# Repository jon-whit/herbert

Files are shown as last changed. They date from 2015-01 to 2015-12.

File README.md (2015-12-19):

Documents
	- this folder contains our documentation including presentations and support material

Electronics
	- this folder contains the datasheets and schematics for the electronic boards we used

Firmware
	- this folder contains the fpga and firmware code

ImageProcessing
	- this folder contains the image processing code and the kcube application

Mechanical 
	- this folder contains the mechanical drawing for parts we designed and datasheets for parts we bought

TestApplication
	- this folder contains the code for our debug gui application we used for testing

Each of these folders contains it's own README explaining in more detail the contents

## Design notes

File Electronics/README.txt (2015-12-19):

This folder contains a directory for each of the electronic boards.  

The directories contain related schematics and datasheets for each part.

We did not design any of these boards.  We only repurposed i/o ports for our purposes.

These documents were used for reference only.

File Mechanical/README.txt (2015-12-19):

This folder contains mechanical drawings or datasheets for each of the mechanical parts we either designed or bought

The parts that we designed were:
	- RC-MECH-01 Socket
	- RC-MECH-02 Sensor Mount
	- RC-MECH-07 Pin
	- RC-MECH-11 Back Plate
	- RC-MECH-20 Bearing Plateform
	- RC-MECH-21 Solenoid Valve Mount

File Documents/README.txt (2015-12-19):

The "Documents" directory contains all of the documents that we created or
collected over the course of this project. This includes presentations, proposals,
and any material that we referenced for the design of our project.

--------
FPGADocs
--------
A directory containing a PDF that we used to help us program the Microblaze
processor on the FPGA.

----------
GroupNotes
----------
A directory that contains group meeting notes between January and February. We
switched over to Hansoft during the summer, and then we started emailing you with
progress updates this semester.

------
Images
------
A directory containing all of the images and models of our system that were used
in our presentations, proposal, and final report.

-------------
Presentations
-------------
Contains our initial presentation (ECE 3992) and our final presentation, along with
the supporting material for these presentations.

------
Videos
------
Contains a few videos highlighting the progress of the system over time.

--------
main.tex
--------
Our final presentation

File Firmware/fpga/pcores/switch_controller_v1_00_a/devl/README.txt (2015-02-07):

TABLE OF CONTENTS
  1) Peripheral Summary
  2) Description of Generated Files
  3) Description of Used IPIC Signals
  4) Description of Top Level Generics

================================================================================
*                             1) Peripheral Summary                            *
================================================================================
Peripheral Summary:

  XPS project / EDK repository               : C:\Git\herbert\Firmware\fpga
  logical library name                       : switch_controller_v1_00_a
  top name                                   : switch_controller
  version                                    : 1.00.a
  type                                       : PLB (v4.6) slave
  features                                   : slave attachment
                                               user s/w registers

Address Block for User Logic and IPIF Predefined Services

  user logic slave space                     : C_BASEADDR + 0x00000000
                                             : C_BASEADDR + 0x000000FF

================================================================================
*                          2) Description of Generated Files                   *
================================================================================
- HDL source file(s)

  hdl/vhdl/switch_controller.vhd

    This is the template file for your peripheral's top design entity. It
    configures and instantiates the corresponding design units in the way you
    indicated in the wizard GUI and hooks it up to the stub user logic where
    the actual functionalites should get implemented. You are not expected to
    modify this template file except certain marked places for adding user
    specific generics and ports.

  vhdl/user_logic.vhd

    This is the template file for the stub user logic design entity, either in
    VHDL or Verilog, where the actual functionalities should get implemented.
    Some sample code snippet may be provided for demonstration purpose.

- XPS interface file(s)

  data/switch_controller_v2_1_0.mpd

    This Microprocessor Peripheral Description file contains information of the
    interface of your peripheral, so that other EDK tools can recognize your
    peripheral.

  data/switch_controller_v2_1_0.pao

    This Peripheral Analysis Order file defines the analysis order of all the HDL
    source files that are used to compile your peripheral.

- ISE project file(s)

  devl/projnav/switch_controller.ise

    This is the ProjNavigator project file. It sets up the needed logical
    libraries and dependent library files for you to help you develop your
    peripheral using ProjNavigator.

  devl/projnav/switch_controller.cli

    This is the TCL command line file used to generate the .ise file.

- XST synthesis file(s)

  devl/synthesis/switch_controller_xst.scr

    This is the XST synthesis script file to compile your peripheral.
    Note: you may want to modify the device part option for your target.

  devl/synthesis/switch_controller_xst.prj

    This is the XST synthesis project file used by the above script file to
    compile your peripheral.

- Driver source file(s)

  src/switch_controller.h

    This is the software driver header template file, which contains address offset of
    software addressable registers in your peripheral, as well as some common masks and
    simple register access macros or function declaration.

  src/switch_controller.c

    This is the software driver source template file, to define all applicable driver
    functions.

  src/switch_controller_selftest.c

    This is the software driver self test example file, which contain self test example
    code to test various hardware features of your peripheral.

  src/Makefile

    This is the software driver makefile to compile drivers.

- Driver interface file(s)

  data/switch_controller_v2_1_0.mdd

    This is the Microprocessor Driver Definition file.

  data/switch_controller_v2_1_0.tcl

    This is the Microprocessor Driver Command file.

- Other misc file(s)

  devl/ipwiz.opt

    This is the option setting file for the wizard batch mode, which should
    generate the same result as the wizard GUI mode.

  devl/README.txt

    This README file for your peripheral.

  devl/ipwiz.log

    This is the log file by operating on this wizard.

================================================================================
*                         3) Description of Used IPIC Signals                  *
================================================================================
For more information (usage, timing diagrams, etc.) regarding the IPIC signals
used in the templates, please refer to the following specifications (under
%XILINX_EDK%\doc for windows or $XILINX_EDK/doc for solaris and linux):
proc_ip_ref_guide.pdf - Processor IP Reference Guide (chapter 4 IPIF)
user_core_templates_ref_guide.pdf - User Core Templates Reference Guide

Bus2IP_Clk
    Synchronization clock provided to the user logic. All IPIC signals are 
    synchronous to this clock. It is identical to the input <bus>_Clk signal of 
    the peripheral. No additional buffering is provided on the clock; it is 
    passed through as is. 

Bus2IP_Reset
    Active high reset for used by the user logic; it is asserted whenever the 
    <bus>_Rst signal asserts or whenever there is a software-programmed reset 
    (if the soft reset block is included). 

Bus2IP_Data
    Write data bus to the user logic. Write data is accepted by the user logic 
    during a write operation by assertion of the write acknowledgement signal 
    and the rising edge of the Bus2IP_Clk. 

Bus2IP_BE
    Byte Enable qualifiers for the requested read or write operation to the user 
    logic. A bit in the Bus2IP_BE set to '1' indicates that the associated byte 
    lane contains valid data. For example, if Bus2IP_BE = 0011, this indicates 
    that byte lanes 2 and 3 contains valid data. 

Bus2IP_RdCE
    Active high chip enable bus to the user logic. These chip enables are 
    asserted only during active read transaction requests with the target 
    address space and in conjunction with the corresponding sub-address within 
    the space. Typically used for user logic readable registers selection. 

Bus2IP_WrCE
    Active high chip enable bus to the user logic. These chip enables are 
    asserted only during active write transaction requests with the target 
    address space and in conjunction with the corresponding sub-address within 
    the space. Typically used for user logic writable registers selection. 

IP2Bus_Data
    Output read data bus from the user logic; data is qualified with the 
    assertion of IP2Bus_RdAck signal and the rising edge of the Bus2IP_Clk. 

IP2Bus_RdAck
    Active high read data qualifier providing the read acknowledgement from the 
    user logic. Read data on the IP2Bus_Data bus is deemed valid at the rising 
    edge of the Bus2IP_Clk and IP2Bus_RdAck asserted high by the user logic. For 
    immediate acknowledgement (such as for a register read), this signal can be 
    tied to '1'. Wait states can be inserted in the transaction by delaying the 
    assertion of the acknowledgement. 

IP2Bus_WrAck
    Active high write data qualifier providing the write acknowledgement from 
    the user logic. Write data on the Bus2IP_Data bus is deemed accepted by the 
    user logic at the rising edge of the Bus2IP_Clk and IP2Bus_WrAck asserted 
    high by the user logic. For immediate acknowledgement (such as for a 
    register write), this signal can be tied to '1'. Wait states can be inserted 
    in the transaction by delaying the assertion of the acknowledgement. 

IP2Bus_Error
    Active high signal indicating the user logic has encountered an error with 
    the requested operation. It is asserted in conjunction with the read/write 
    acknowledgement signal(s). 

================================================================================
*                     4) Description of Top Level Generics                     *
================================================================================
C_BASEADDR/C_HIGHADDR
    These two generics are used to define the memory mapped address space for
    the peripheral registers, including Soft Reset register, Interrupt Source
    Controller registers, Read/Write FIFO control/data registers, user logic
    software accessible registers and etc., but excluding those user logic
    memory spaces if ever existed. When instantiation, the address space
    size determined by these two generics must be a power of 2 (e.g. 2^k =
    C_HIGHADDR - C_BASEADDR + 1), a factor of C_BASEADDR and larger than the
    minimum size as indicated in the template.

C_SPLB_AWIDTH
    This is the slave interface address bus width for Processor Local Bus
    version 4.6 (PLBv46). Value can be assigned automatically by EDK
    tooling during system creation.

C_SPLB_DWIDTH
    This is the slave interface data bus width for Processor Local Bus
    version 4.6 (PLBv46). Value can be assigned automatically by EDK
    tooling during system creation.

C_SPLB_NUM_MASTERS
    This indicates to the slave interface the number of PLBv46 masters
    present. Value can be assigned automatically by EDK tooling during
    system creation.

C_SPLB_MID_WIDTH
    This indicates to the slave interface the number of bits required
    for the PLB_masterID input bus. It is an integer value equal to
    log2(C_SPLB_NUM_MASTERS). Value will be assigned automatically by
    EDK tooling during system creation.

C_SPLB_NATIVE_DWIDTH
    This indicates to the slave interface the native bit width of the
    internal data bus of the peripheral. Some peripheral will require
    the value of this parameter to be fixed, while others might have
    selectable native data widths.

C_SPLB_P2P
    This indicates to the slave interface when it is exclusively attached
    to a PLBv46 bus via a Point to Point interconnect scheme. In this
    scenario, the slave interface may be able to reduce resource utilization
    by eliminating address decode function and modifying interface behavior
    to allow for a reduction in latency.

C_SPLB_SUPPORT_BURSTS
    This indicates to the associated PLBv46 bus that this slave interface
    support burst transfers to improve performance.

C_SPLB_SMALLEST_MASTER
    This indicates the smallest native data width of any master on the
    corresponding PLBv46 bus that may access the slave interface. It allows
    optimizations within the slave interface logic if narrower masters don't
    have to be supported for that application.

C_SPLB_CLK_PERIOD_PS
    This is the period of the PLBv46 bus clock (in picoseconds) for the
    corresponding PLBv46 slave interface attachment. It has been defined
    for use by peripheral that needs to know the bus clock rate to improve
    certain functions such as internal timers.

C_INCLUDE_DPHASE_TIMER
    This indicates if the data phase timer is used or not. The value of
    0 will exclude the timer.  The value of 1 includes the timer.
    If C_INCLUDE_DPHASE_TIMER = 1 and after 128 SPLB_Clk cycles, as
    measured from the assertion of Sl_AddrAck, the User IP does not
    respond with either an IP2Bus_RdAck or IP2Bus_WrAck the 
    plbv46_slave_single will de-assert the User IP cycle request
    signals, Bus2IP_CS and Bus2IP_RdCE or Bus2IP_WrCE, and will assert
    Sl_rdDAck with Sl_rdDBus=zero for a read cycle or Sl_wrDAck for
    a write cycle. This will gracefully terminate the cycle. Note 
    that the requesting master will have no knowledge that the data
    phase of the PLB request was terminated in this manner.

C_FAMILY
    This is to set the target FPGA architecture, s.t. virtex5, etc.

================================================================================
*          5) Location to documentation of dependent libraries                 *
*                                                                              *
*   In general, the documentation is located under:                            *
*   $XILINX_EDK/hw/XilinxProcessorIPLib/pcores/$libName/doc                    *
*                                                                              *
================================================================================
proc_common_v2_00_a
	No documentation for this library

plbv46_slave_single_v1_00_a
	C:\Git\herbert\Firmware\fpga\C:\Xilinx\10.1\EDK\hw\XilinxProcessorIPLib\pcores\plbv46_slave_single_v1_00_a\doc\plbv46_slave_single.pdf

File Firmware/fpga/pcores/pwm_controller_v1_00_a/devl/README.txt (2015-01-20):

TABLE OF CONTENTS
  1) Peripheral Summary
  2) Description of Generated Files
  3) Description of Used IPIC Signals
  4) Description of Top Level Generics

================================================================================
*                             1) Peripheral Summary                            *
================================================================================
Peripheral Summary:

  XPS project / EDK repository               : C:\Development\Sandbox\Projects\PlateCycler\Alpha\Firmware\S3DevBoard
  logical library name                       : pwm_controller_v1_00_a
  top name                                   : pwm_controller
  version                                    : 1.00.a
  type                                       : PLB (v4.6) slave
  features                                   : slave attachment
                                               interrupt control
                                               user s/w registers

Address Block for User Logic and IPIF Predefined Services

  user logic slave space                     : C_BASEADDR + 0x00000000
                                             : C_BASEADDR + 0x000000FF
  interrupt control space                    : C_BASEADDR + 0x00000100
                                             : C_BASEADDR + 0x000001FF

================================================================================
*                          2) Description of Generated Files                   *
================================================================================
- HDL source file(s)

  hdl/vhdl/pwm_controller.vhd

    This is the template file for your peripheral's top design entity. It
    configures and instantiates the corresponding design units in the way you
    indicated in the wizard GUI and hooks it up to the stub user logic where
    the actual functionalites should get implemented. You are not expected to
    modify this template file except certain marked places for adding user
    specific generics and ports.

  vhdl/user_logic.vhd

    This is the template file for the stub user logic design entity, either in
    VHDL or Verilog, where the actual functionalities should get implemented.
    Some sample code snippet may be provided for demonstration purpose.

- XPS interface file(s)

  data/pwm_controller_v2_1_0.mpd

    This Microprocessor Peripheral Description file contains information of the
    interface of your peripheral, so that other EDK tools can recognize your
    peripheral.

  data/pwm_controller_v2_1_0.pao

    This Peripheral Analysis Order file defines the analysis order of all the HDL
    source files that are used to compile your peripheral.

- ISE project file(s)

  devl/projnav/pwm_controller.ise

    This is the ProjNavigator project file. It sets up the needed logical
    libraries and dependent library files for you to help you develop your
    peripheral using ProjNavigator.

  devl/projnav/pwm_controller.cli

    This is the TCL command line file used to generate the .ise file.

- XST synthesis file(s)

  devl/synthesis/pwm_controller_xst.scr

    This is the XST synthesis script file to compile your peripheral.
    Note: you may want to modify the device part option for your target.

  devl/synthesis/pwm_controller_xst.prj

    This is the XST synthesis project file used by the above script file to
    compile your peripheral.

- Driver source file(s)

  src/pwm_controller.h

    This is the software driver header template file, which contains address offset of
    software addressable registers in your peripheral, as well as some common masks and
    simple register access macros or function declaration.

  src/pwm_controller.c

    This is the software driver source template file, to define all applicable driver
    functions.

  src/pwm_controller_selftest.c

    This is the software driver self test example file, which contain self test example
    code to test various hardware features of your peripheral.

  src/Makefile

    This is the software driver makefile to compile drivers.

- Driver interface file(s)

  data/pwm_controller_v2_1_0.mdd

    This is the Microprocessor Driver Definition file.

  data/pwm_controller_v2_1_0.tcl

    This is the Microprocessor Driver Command file.

- Other misc file(s)

  devl/ipwiz.opt

    This is the option setting file for the wizard batch mode, which should
    generate the same result as the wizard GUI mode.

  devl/README.txt

    This README file for your peripheral.

  devl/ipwiz.log

    This is the log file by operating on this wizard.

================================================================================
*                         3) Description of Used IPIC Signals                  *
================================================================================
For more information (usage, timing diagrams, etc.) regarding the IPIC signals
used in the templates, please refer to the following specifications (under
%XILINX_EDK%\doc for windows or $XILINX_EDK/doc for solaris and linux):
proc_ip_ref_guide.pdf - Processor IP Reference Guide (chapter 4 IPIF)
user_core_templates_ref_guide.pdf - User Core Templates Reference Guide

Bus2IP_Clk
    Synchronization clock provided to the user logic. All IPIC signals are 
    synchronous to this clock. It is identical to the input <bus>_Clk signal of 
    the peripheral. No additional buffering is provided on the clock; it is 
    passed through as is. 

Bus2IP_Reset
    Active high reset for used by the user logic; it is asserted whenever the 
    <bus>_Rst signal asserts or whenever there is a software-programmed reset 
    (if the soft reset block is included). 

Bus2IP_Data
    Write data bus to the user logic. Write data is accepted by the user logic 
    during a write operation by assertion of the write acknowledgement signal 
    and the rising edge of the Bus2IP_Clk. 

Bus2IP_BE
    Byte Enable qualifiers for the requested read or write operation to the user 
    logic. A bit in the Bus2IP_BE set to '1' indicates that the associated byte 
    lane contains valid data. For example, if Bus2IP_BE = 0011, this indicates 
    that byte lanes 2 and 3 contains valid data. 

Bus2IP_RdCE
    Active high chip enable bus to the user logic. These chip enables are 
    asserted only during active read transaction requests with the target 
    address space and in conjunction with the corresponding sub-address within 
    the space. Typically used for user logic readable registers selection. 

Bus2IP_WrCE
    Active high chip enable bus to the user logic. These chip enables are 
    asserted only during active write transaction requests with the target 
    address space and in conjunction with the corresponding sub-address within 
    the space. Typically used for user logic writable registers selection. 

IP2Bus_Data
    Output read data bus from the user logic; data is qualified with the 
    assertion of IP2Bus_RdAck signal and the rising edge of the Bus2IP_Clk. 

IP2Bus_RdAck
    Active high read data qualifier providing the read acknowledgement from the 
    user logic. Read data on the IP2Bus_Data bus is deemed valid at the rising 
    edge of the Bus2IP_Clk and IP2Bus_RdAck asserted high by the user logic. For 
    immediate acknowledgement (such as for a register read), this signal can be 
    tied to '1'. Wait states can be inserted in the transaction by delaying the 
    assertion of the acknowledgement. 

IP2Bus_WrAck
    Active high write data qualifier providing the write acknowledgement from 
    the user logic. Write data on the Bus2IP_Data bus is deemed accepted by the 
    user logic at the rising edge of the Bus2IP_Clk and IP2Bus_WrAck asserted 
    high by the user logic. For immediate acknowledgement (such as for a 
    register write), this signal can be tied to '1'. Wait states can be inserted 
    in the transaction by delaying the assertion of the acknowledgement. 

IP2Bus_Error
    Active high signal indicating the user logic has encountered an error with 
    the requested operation. It is asserted in conjunction with the read/write 
    acknowledgement signal(s). 

IP2Bus_IntrEvent
    The IP2Bus_IntrEvent bus is an output from the user logic to the IPIF that 
    consists of interrupt event signals to be detected and latched inside the 
    IPIF. 

================================================================================
*                     4) Description of Top Level Generics                     *
================================================================================
C_BASEADDR/C_HIGHADDR
    These two generics are used to define the memory mapped address space for
    the peripheral registers, including Soft Reset register, Interrupt Source
    Controller registers, Read/Write FIFO control/data registers, user logic
    software accessible registers and etc., but excluding those user logic
    memory spaces if ever existed. When instantiation, the address space
    size determined by these two generics must be a power of 2 (e.g. 2^k =
    C_HIGHADDR - C_BASEADDR + 1), a factor of C_BASEADDR and larger than the
    minimum size as indicated in the template.

C_SPLB_AWIDTH
    This is the slave interface address bus width for Processor Local Bus
    version 4.6 (PLBv46). Value can be assigned automatically by EDK
    tooling during system creation.

C_SPLB_DWIDTH
    This is the slave interface data bus width for Processor Local Bus
    version 4.6 (PLBv46). Value can be assigned automatically by EDK
    tooling during system creation.

C_SPLB_NUM_MASTERS
    This indicates to the slave interface the number of PLBv46 masters
    present. Value can be assigned automatically by EDK tooling during
    system creation.

C_SPLB_MID_WIDTH
    This indicates to the slave interface the number of bits required
    for the PLB_masterID input bus. It is an integer value equal to
    log2(C_SPLB_NUM_MASTERS). Value will be assigned automatically by
    EDK tooling during system creation.

C_SPLB_NATIVE_DWIDTH
    This indicates to the slave interface the native bit width of the
    internal data bus of the peripheral. Some peripheral will require
    the value of this parameter to be fixed, while others might have
    selectable native data widths.

C_SPLB_P2P
    This indicates to the slave interface when it is exclusively attached
    to a PLBv46 bus via a Point to Point interconnect scheme. In this
    scenario, the slave interface may be able to reduce resource utilization
    by eliminating address decode function and modifying interface behavior
    to allow for a reduction in latency.

C_SPLB_SUPPORT_BURSTS
    This indicates to the associated PLBv46 bus that this slave interface
    support burst transfers to improve performance.

C_SPLB_SMALLEST_MASTER
    This indicates the smallest native data width of any master on the
    corresponding PLBv46 bus that may access the slave interface. It allows
    optimizations within the slave interface logic if narrower masters don't
    have to be supported for that application.

C_SPLB_CLK_PERIOD_PS
    This is the period of the PLBv46 bus clock (in picoseconds) for the
    corresponding PLBv46 slave interface attachment. It has been defined
    for use by peripheral that needs to know the bus clock rate to improve
    certain functions such as internal timers.

C_FAMILY
    This is to set the target FPGA architecture, s.t. virtex5, etc.

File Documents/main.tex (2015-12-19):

% pre-amble section
\documentclass[final, letterpaper, 10 pt, conference, twocolumn]{IEEEtran}

\usepackage[utf8]{inputenc}
\usepackage{geometry}
\usepackage{hyperref}
\usepackage{graphicx}
\graphicspath{ {Images/} }
\usepackage{listings}
\usepackage{xcolor}
\usepackage{fancyvrb}
\usepackage[backend=bibtex]{biblatex}

\bibliography{references.bib}

\lstdefinestyle{DOS}
{
    backgroundcolor=\color{black},
    basicstyle=\scriptsize\color{white}\ttfamily
}

\title{Herbert\\Autonomous Robotic Rubik's Cube Solver}
\author{
    Jonathan Whitaker, Dylan Lytle, Matt Frandsen, Li Lao\\
    \textit{Dept. of Electrical and Computer Engineering, University of Utah}\\
}

\date{December 2015}
% end of pre-amble

% document content
\begin{document}

\maketitle

\begin{abstract}
Project Herbert is an autonomous robotic Rubik's Cube solver that is composed of a complex network of mechanical and electrical devices. In this project our team interfaced with these complex mechanical and electrical devices so as to design and create an autonomous robot that is capable of solving a Rubik's cube within two minutes of time.  This project is an integration of various technologies including: mechanical actuators, electrical stepper motors, single-board computers, field-programmable gate arrays, and video cameras.
\end{abstract}

\section{Introduction}
\label{sec:intro}
The goal of this project was to create an autonomous robotic Rubik's Cube solver through the integration of several components. The main components integrated into our project include video cameras, electrical stepper motors, mechanical actuators, a single-board computer (SBC), and field-programmable gate arrays (FPGAs). A video camera connects to the computer through standard universal serial bus (USB) 2.0 protocol \cite{USB2.0}. The video camera is responsible for capturing the initial configuration of the Rubik's Cube, and the single board computer is responsible for processing the video frame information and generating a matrix model for the initial state of the cube. After generating a matrix model for the initial cube, the computer applies Kociemba's algorithm \cite{Kociemba} (an optimal algorithm used to solve a Rubik's Cube) to generate a solution sequence that can be processed sequentially. The solution sequence that Kociemba's algorithm returns is in the standard notation used in Rubik's Cube discussion and theory (see Appendix \ref{sec:Appendix A}). As each solution sequence is processed, the computer communicates through an RS232 serial connection to an FPGA control board which drives the mechanical actuations and stepper motor rotations needed to physically manipulate the cube. The FPGA acts as a system control board and is responsible for controlling the actions of two motor control boards and a relay board used to trigger the mechanical actuators. An overview of this process can be found below in Fig. \ref{fig:System Block Diagram}.

\begin{figure*}[!ht]
\centering

\caption{Herbert Block Diagram}
\label{fig:System Block Diagram}
\end{figure*}

\begin{figure}[!ht]
\centering

\caption{Initial ideal cube image capture}
\label{fig:Camera Positioning}
\end{figure}

\section{Software Implementation}
\label{sec:Software Implementation}
The single board computer in our system operates a software stack composed of Python, Cython, and OpenCV. We utilized a 3rd party Python library called \textit{pyflycapture2} \cite{pyflycapture2} to capture images from the camera that was provided to us by Point Grey Research. Once the images of the cube are captured, we apply color recognition and categorization using OpenCV-Python \cite{OpenCVPython}. The characterization phase in OpenCV generates a matrix model of the Rubik's cube. We pass this matrix model on to an application called Kcube to generate a solution sequence needed to solve the cube permutation. We go into each these components in more detail in the next few sections.

\subsection{Image Processing}
The image processing aims to capture the initial state of the cube using a camera. The criteria for evaluating the success of the image processing implementation is robustness and speed of the algorithm.

\begin{figure}[!hb]
\centering
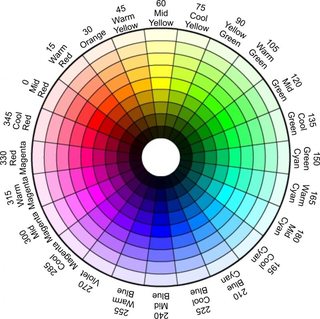
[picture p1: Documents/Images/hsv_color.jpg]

\caption{HSV color wheel}
\label{fig:HSV}
\end{figure}

\subsubsection{Point Grey Camera and FlyCapture Software Development Kit}
We interfaced with the cameras using Point Grey's API, which was provided to us through the FlyCapture software development kit (SDK) \cite{FlyCapture}. The FlyCapture SDK was implemented in C. Since we chose to use Python as our base language, we had to use Cython, an optimized static compiler for C extensions in Python. We use Cython to bind the C functions within the FlyCapture API to Python functions.  The FlyCapture SDK  provided us with a large amount of configurability, and it gave us a flexible interface for which the cameras settings could be adjusted to enhance capturing mode and synchronizing image buffer retrieval.

We initially had planned to use two cameras, each connected to the SBC through a standard USB 2.0 connection. Each one of these cameras was going to be responsible for capturing exactly three of the six faces of the cube with a view like that shown in Fig. \ref{fig:Camera Positioning}. However, as construction of the main frame of our project came to a close, we soon realized that various parts of the mechanical system obscured the view of a large majority of the facelets on the three faces. On top of this, we also experienced challenges dealing with color recognition in ambient lighting. Because of these challenges we decided that our original camera configuration was not ideal.

We decided to compromise and use a single camera configuration. A single camera is used to capture the entire state of a Rubik's Cube. The single camera was best positioned like that shown in Fig. \ref{fig:Obscured Cube}. A static mechanical rotation sequence is used to capture the cube in various configurations until all of the facelets on the cube are captured. The cube is then returned to its original state, and the collection of images are saved off for facelet characterization.

\subsubsection{Cube Orientation} 
The pixel region of each of the facelets  must be identified for color recognition. We initially planned on using a combination of grayscale conversion and contour filtering to dynamically detect a bounding contour around each of the facelets. However, the dynamic approach to identifying a facelet pixel region proved to be difficult due to the lack of vision of the cube. The arm assemblies were too obtrusive to capture a clean image (see Fig. \ref{fig:Obscured Cube}).

Because the camera and the Rubik's Cube remains fixed inside the mechanical frame, we decided to implement a static solution. Through a GUI interface, a static polygon for each of the facelets was defined. Each of the static polygons creates a bounding rectangle around a facelet pixel region. The static solution that we adopted proved to be consistent, but it necessitated high maintenance. Each of the static polygons must be redefined each time the camera position changes or if a mechanical change affects the orientation of the cube. If we were to continue on with this project, this is one aspect that we could improve. It would be nice to implement a robust dynamic approach.

\begin{figure}[!h]
\centering
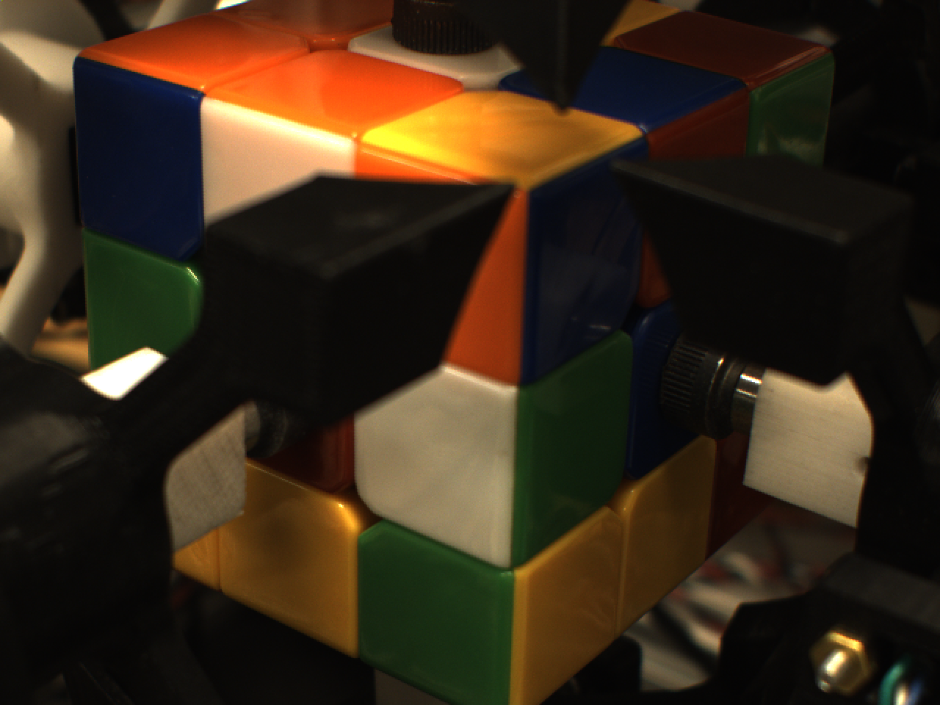
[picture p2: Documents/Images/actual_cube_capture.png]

\caption{Obscured cube image capture}
\label{fig:Obscured Cube}
\end{figure}

\subsubsection{Color Space}
Lighting condition severally affects the robustness of the color recognition algorithm. Color values on a Rubik's Cube facelet drastically change if the facelet is reflective or if a shadow is cast upon it. This proved to be challenging for us. However, we were able to maintain a consistent lighting around the mechnical frame to mitigate a majority of these problems. We were very confident in the color recognition algorithm under normal lighting conditions. During demo day, we solved over 24 Rubik's Cubes without failure.

Choosing a color space that was robust to lighting conditions was critical to enabling a robust color recognition algorithm. Several color spaces such as RGB, CMYK, and HSV were examined. The HSV color space provided the best consistency under various lighting conditions. The three components of the HSV color space are hue, saturation, and value. The hue component describes the similarity of the color to an unique hue: red, green, blue, and yellow as shown in Fig. \ref{fig:HSV}. The saturation component measures the intensity or ``colorfulness" of the specific hue. Finally, the value measures the brightness of the color value. HSV is ideal for developing a robust color recognition because shadows and high gloss merely change the value component of the color without affecting the hue and saturation component of the color. Additionally, the hue component can be used to distinctly distinguish each of the primary colors such as red, green, and blue that are found on a Rubik's Cube facelet.

\begin{figure}[!ht]
\centering
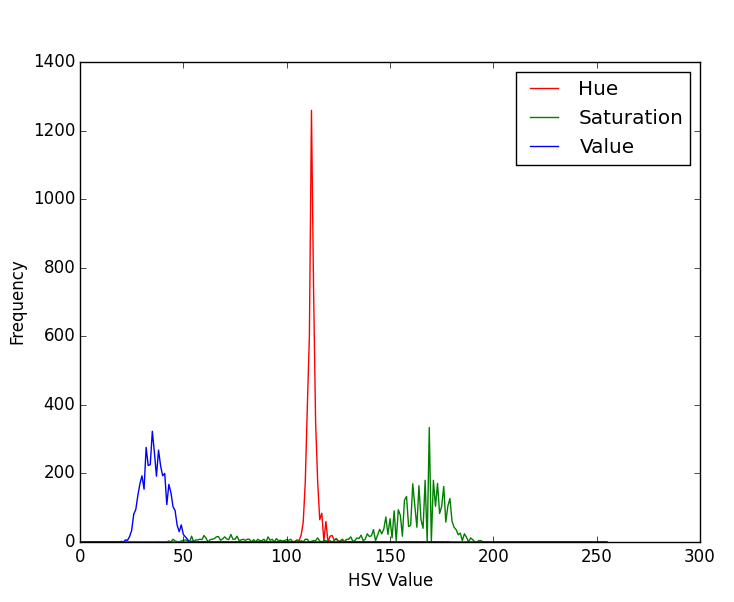
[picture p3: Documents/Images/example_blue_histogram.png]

\caption{Example HSV color histogram for blue}
\label{fig:Example Histogram}
\end{figure}

\begin{table}[!ht]
\caption{HSV color ranges}
\label{table:color ranges}
\centering
\begin{tabular}{|c|c|c|}
\hline
\textbf{COLOR} & \textbf{HUE} & \textbf{SATURATION} \\ \hline
WHITE          & 25 - 58  & 0 - 139               \\ \hline
RED            & 1  - 12     & 0 - 255            \\ \hline
BLUE           & 200 - 280   & 0 - 255              \\ \hline
GREEN          & 80 - 120   & 0 - 255            \\ \hline
ORANGE         & 15 - 20     & 0 - 255         \\ \hline
YELLOW         & 25 - 58   & 140 - 255            \\ \hline
\end{tabular}
\end{table}

\subsubsection{Categorization Algorithm}
After identifying a bounding contour around each of the facelets, a categorization algorithm was used to determine the color contained within the bounding rectangle. Each image was first converted to the HSV color space. The hue and saturation components of each pixel value is then used to categorize the color. Several color histograms such as the one shown in Fig. \ref{fig:Example Histogram} were constructed for each facelet and were used to determine the ranges of each HSV component in order to categorize a single facelet color. For example, the histogram shown in Fig. \ref{fig:Example Histogram} was constructed for a blue facelet. The hue values range between 100 to 130 and the saturation values ranges from 150 to 180. Our analysis led to the resulting HSV ranges shown in Table. \ref{table:color ranges}.

Based on these color ranges, the categorization algorithm can be implemented based on the average of all the pixel values in the facelet region or the frequency of each pixel value. A categorization algorithm based on the average of HSV values proved to be quick, but it was also error-prone due to outliers. A categorization algorithm based on frequency of each HSV component proved to be more robust, but less optimized. Our final implementation computes a histogram of the facelet pixel region using OpenCV. Based on the histogram, the frequency of each of the facelet colors is determined. The highest frequency of a facelet color determines the color that facelet is binned into.

Our initial trivial algorithm that we implemented took approximately a minute to categorize each facelet, because of the unoptimized looping in Python and hardware limitations. After several iterative optimizations using the OpenCV library, the overall color categorization time was reduced to approximately three seconds.  In the future, the categorization can still be optimized for both robustness and speed. For example, the image resolution or the overall pixel region can be reduced to improve performance. Additionally, a filtering algorithm can be used to reduce the effects on abnormal lighting. 

\subsection{Kcube and the Solution Sequence}
\begin{figure*}[!ht]
\begin{center}
\begin{BVerbatim}
             |************|
             |*U1**U2**U3*|
             |************|
             |*U4**U5**U6*|
             |************|
             |*U7**U8**U9*|
             |************|
|************|************|************|************|
|*L1**L2**L3*|*F1**F2**F3*|*R1**R2**F3*|*B1**B2**B3*|
|************|************|************|************|
|*L4**L5**L6*|*F4**F5**F6*|*R4**R5**R6*|*B4**B5**B6*|
|************|************|************|************|
|*L7**L8**L9*|*F7**F8**F9*|*R7**R8**R9*|*B7**B8**B9*|
|************|************|************|************|
             |************|
             |*D1**D2**D3*|
             |************|
             |*D4**D5**D6*|
             |************|
             |*D7**D8**D9*|
             |************|
\end{BVerbatim}
\end{center}
\caption{Rubik's Cube matrix representation}
\label{fig:matrix layout}
\end{figure*}

\begin{table}[!ht]
\caption{Cubelet color to ASCII character mapping}
\label{table:cubelet representation}
\centering
\begin{tabular}{|c|c|}
\hline
\textbf{COLOR} & \textbf{CHARACTER} \\ \hline
WHITE          & `W'              \\ \hline
RED            & `R'              \\ \hline
BLUE           & `B'              \\ \hline
GREEN          & `G'              \\ \hline
ORANGE         & `O'              \\ \hline
YELLOW         & `Y'              \\ \hline
\end{tabular}
\end{table}

\label{sec:Kcube}
Kcube is a C++ application developed by Greg Schmidt that utilizes Kociemba's two-phase algorithm which uses two stages of an iterative depth first search algorithm \cite{TheTwo-PhaseAlgorithm}. We utilized the Kcube application to generate the solution sequence needed to solve the Rubik's Cube that was captured during the image processing phase. The matrix model generated from the image processing phase allows us to provide Kcube's command-line interface with the cube representation needed to generate a solution sequence. Kcube's command-line interface takes six parameters, one for each face of the cube. The values for these parameters are the color characters at each of the cubelet locations for that face (as seen in Fig. \ref{fig:matrix layout}). For example, to solve the scrambled cube shown in Fig. \ref{fig:scrambled cube} you invoke Kcube with the following command:

\begin{lstlisting}[style=DOS]
c:>kcube L:GGWWOWBRB
         F:GWGBGYWBO
         U:YOOOWYROY
         D:ORGWYYYRB
         R:OGBBRYWRR
         B:YBROBGWGR
\end{lstlisting}

Kcube processes the input parameters and generates a sequence of twenty-three or less moves (see Appendix \ref{sec:fundamental moves}) that, when applied to the cube, will solve the cube. Each move is mapped to a unique character or set of characters (see Table \ref{table:moves table}), and these characters are transmitted over an RS232 serial connection to the FPGA control board, at which point the control board takes responsibility for controlling the electro-mechanical stepper motors and mechanical actuators needed to physically manipulate the cube.

\begin{figure}[!hb]
\centering

\caption{A scrambled cube}
\label{fig:scrambled cube}
\end{figure}

\begin{table}[!ht]
\caption{Cube moves to character set mapping}
\label{table:moves table}
\centering
\begin{tabular}{|c|c|c|c|c|c|}
\hline
\textbf{MOVE} & \textbf{CHAR} & \textbf{MOVE} & \textbf{CHAR} & \textbf{MOVE} & \textbf{CHAR} \\ \hline
F             & F              & R             & R              & D             & D             \\ \hline
F'            & Fb              & R'            & Rb              & D'            & Db            \\ \hline
F2            & F2              & R2            & R2              & D2            & D2             \\ \hline
L             & L              & U             & U             & B             & B             \\ \hline
L'            & Lb              & U'            & Ub             & B'            & Bb             \\ \hline
L2            & L2              & U2            & U2             & B2            & B2             \\ \hline
\end{tabular}
\end{table}

\section{Hardware Implementation}
\subsection{Mechanical Actuators}
\label{sec:Mechanical Actuators}
Herbert employs a six arm design to physically manipulate the cube. One arm for each face of the cube. In order to achieve a six arm design, each arm actuates in and out so as to avoid conflict
with the other arms. This actuation process is a time critical component of
the design.  We initially planned on implementing the
arm actuation with motors.  However, preliminary testing showed that using
motors to convert rotary motion into linear motion is too slow, and using a linear motor
actuator is too costly. We decided that pneumatic actuation is the solution to this problem.  Each of the arms is attached to a double action pneumatic air cylinder as show in Fig. \ref{fig:Pneumatic Air Cylinder}.

The FPGA control board is responsible for controlling a relay control board (see Fig. \ref{fig:System Block Diagram}) which controls coaxial pairs of air cylinders. The actuation distance for each control arm is fixed. The coaxial pairs of arms are kept in an extended or retracted position, depending on the current move being executed. Potential optimizations and more stable cube manipulations  are obtained by simultaneously extending and retracting coaxial pairs of arms. The linear actuation motion allows a coaxial pair of
arms to extend, thus encasing two sides of the cube in the sockets of the arms. After a pair of arms extend,
a stepper motor spins the arm corresponding to the appropriate move from the solution sequence (see section \ref{sec:Stepper Motors}). Each air cylinder is provided approximately 40-60 psi supplied from an air compressor. To protect against any arm collisions, only one pair of arms is in the extended position at any given time.

Initially our design incorporated mechanical switches that would be triggered by physical contact of the arm assembly.  These switches were mounted on the assembly in such a way that contact would occur in either the extended or retracted arm positions.  The goal of the switch based design was to remove an element of manual timing approximation.  By using the switches we would know the position of each arm at all times.  Taking advantage of this, there would be a much smaller hard coded delay, or potentially no delay.  However, due to time constraints as well as accuracy issues because of inconsistent and difficult mounting, we chose not to implement the switches in the final design.   
 
If we were to continue the project there are many improvements and optimizations that could be made. The first optimization would be to implement the switch design we initially planned on.  Improving the robustness of the switches would help reduce the time the mechanical motion takes. This would reduce the overall time to completion, because the mechanical motion is the most time intensive component of the solution. 
Another mechanical optimization that would help reduce the time to completion is to modify the arm.  The image processing was a very difficult component of this project, because the arm assembly was obtrusive to the view of the cube for the cameras.  Our thought is to remove two of the four prongs of each arm.  This modification would give the cameras a more clear view of the cube, as well as potentially giving us the ability to actuate in and out more quickly, because potential arm collisions would be reduced.

\begin{figure}[!ht]
\centering
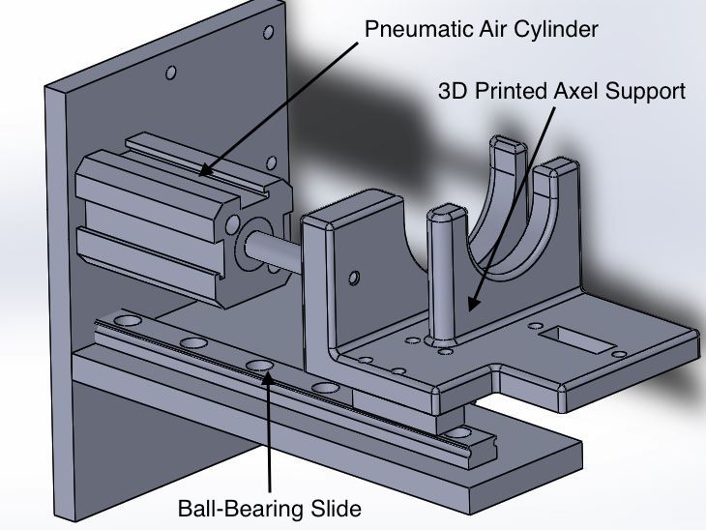
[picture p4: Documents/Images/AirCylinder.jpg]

\caption{Pneumatic Air Cylinder and 3D Printed Axel Support}
\label{fig:Pneumatic Air Cylinder}
\end{figure}

\subsection{Electro-mechanical Stepper Motors}
\label{sec:Stepper Motors}
Each actuating arm has a stepper motor which is responsible for rotating a single face. A stepper motor rotates a face either 90 degrees or 180 degrees clockwise or counter-clockwise based on the solution move that is being processed (as specified in Appendix \ref{sec:Appendix A}). A 3D printed axle (as seen Fig. \ref{fig:Stepper Motor Arm}) is fastened to the stepper motors. This axle twists a 3D printed arm piece in order to spin a face of the Rubik's Cube.

\begin{figure}[!ht]
\centering
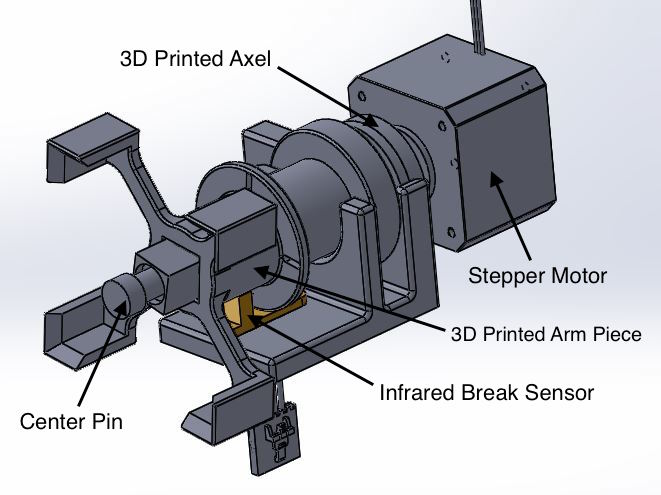
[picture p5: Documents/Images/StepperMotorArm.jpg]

\caption{Stepper Motor Arm Assembly}
\label{fig:Stepper Motor Arm}
\end{figure}

Each stepper motor is driven by a motor control board which is controlled by the FPGA control board (see Fig. \ref{fig:System Block Diagram}). The motor control boards contain a motor driver chip for each stepper motor. The FPGA control board is responsible for controlling the angular and temporal timing of each stepper motor rotation.

\subsection{Infrared Break Sensors}
\label{sec:Infrared Break Sensors}
Rotations must end at a 90 degree angle so as to not interrupt the rotation of another arm.  These exact angles are hard to accomplish by counting steps, because it is difficult to detect whether steps are skipped.  To compensate for this we used infrared break sensors like that shown in Fig. \ref{fig:Infrared Break Sensor}. Each arm assembly has an infrared sensor (see Fig. \ref{fig:Stepper Motor Arm}). The infrared sensor is broken at all angles that are not a multiple of 90 degrees. These break sensors are monitored and controlled through the motor control boards.

\begin{figure}[!ht]
\centering
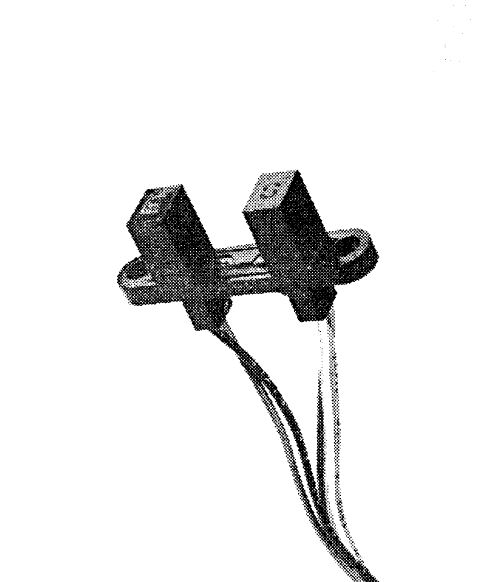
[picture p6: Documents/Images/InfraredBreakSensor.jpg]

\caption{Infrared Break Sensor}
\label{fig:Infrared Break Sensor}
\end{figure}

\subsection{Arm Progression}
\label{sec:Arm Progression}
The 3D printed arm piece at the end of each arm assembly (see Fig. \ref{fig:Stepper Motor Arm}) underwent a great progression. Fig. \ref{fig:Arm Progression} highlights the progression of the arm pieces from left to right. The first iteration was a simple arm that had a square socket and connected directly to the stepper motor without any intermediate axel piece.  The inner part of the socket had chamfered edges to correct for any error in alignment.  The second iteration included tabs for break sensor detection, and it was elongated to accommodate the length of the center pin.  We also modified the socket into four prongs. This allowed better visibility of the cube for the image processing. In the last arm revision we changed from tabbed break sensor detection to slits. This improvement allowed more precise angle detection.  We also shortened the arm, added more chamfered edges for minor alignment error corrections, and included slight height changes to fit the slider piece and circular cutouts to avoid arm collisions.

\begin{figure}[!ht]
\centering
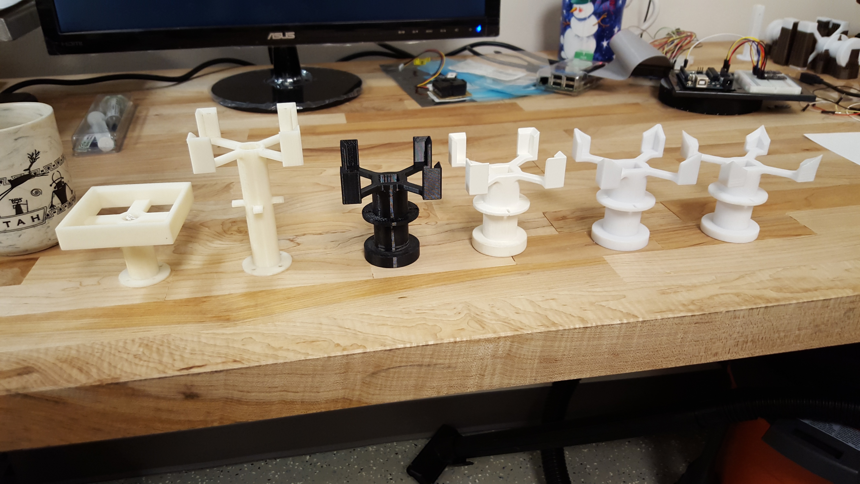
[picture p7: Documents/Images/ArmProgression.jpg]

\caption{Arm Progresssion}
\label{fig:Arm Progression}
\end{figure}

\section{Firmware}
\label{sec:Firmware}
The firmware stemmed from code received from BioFire.  Much of the code provided was only used as a skeleton, and was modified to implement our design.
Table \ref{table:CMDS} outlines the commands we used for this project. For brevity only the main command "ExecuteMoves" will be described, for details on the other commands see  
table \ref{table:CMDS}.  "ExecuteMoves" is the main command that performs the solution sequence generated by Kcube.  Each move is encoded with a specified face(U,F,R,D,B,L) and an optional component either a 'b' indicating a counter-clockwise rotation, or a '2' indicating the move to execute a half turn instead of a quarter turn.  A detailed state diagram outlining this process is shown in Fig.  \ref{fig:ExecuteMoves}

\begin{figure}[!h]
\centering
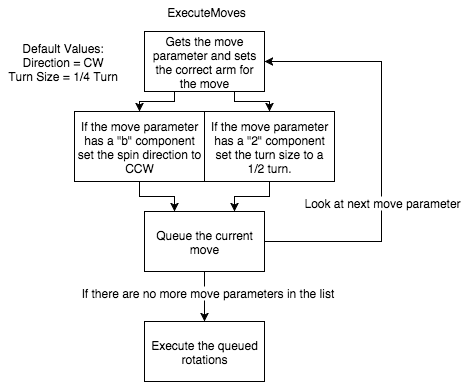
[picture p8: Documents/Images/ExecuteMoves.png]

\caption{"ExecuteMoves" State Diagram}
\label{fig:ExecuteMoves}
\end{figure}

\begin{table*}[!ht]
\caption{Firmware Commands}
\label{table:CMDS}
\resizebox{\textwidth}{!}{\begin{tabular}{|l|c|l|}
\hline
\textbf{Command} & \textbf{Parameters} & \textbf{Description}                                                                                        	                  \\ \hline

ActuateArm           & 1 	     & Toggles the relay board to control the pneumatic actuations of coaxial pairs of arms.                     \\ \hline
	     
DisableMotors       & 0 	     & This command disables the motors.  \\ \hline
				     
TimingTest             & 0 	     & Perform an actuation and spin motion for time testing.  \\ \hline

Abort                      & 0 	     & Halts all motion and clears buffers holding the solution sequence.                    \\ \hline   

MoveRelative         & 2 	     & Manually spin the arm by moving the specified stepper motor the given number of steps.                  \\ \hline      
                                                                                 
MR                         & 2 	     & Equivalent to MoveRelative just a shortened alias.                      \\ \hline
                                                 
GetRawSwitches   & 0 	     & Gets all of the current values for all of the switches.                      \\ \hline   
                                                                                      
GetRawSensors    & 0 	     & Gets all of the current values for all of the break sensors.                       \\ \hline
	     
GetSwitch             & 1            & Gets the current value for the specified switch.                      \\ \hline  
		                                     
GetSensor            & 1           & Gets the current value for the specified break sensor.                      \\ \hline
                                                 
ExecuteMoves     & Variable & Performs the correct actuation and spin sequence for each of the moves provided.                    \\ \hline  
                                                                                      
IsIdle                    & 0           &  Queries the motion state machine to determine if motion is still in progress.                   \\ \hline
                                                 
InitArms               & 0           & Spins each arm until its corresponding break sensor is not blocked.                    \\ \hline                                                                           
\end{tabular}}
\end{table*}

\section{Required Resources}
Table \ref{table:BOM} is the bill of materials (BOM) needed to realize this project. This BOM defines the main materials needed to realize the system as outlined in Fig. \ref{fig:System Block Diagram}.
Many of the components that we used were donated to us by industry sponsors. The components that were donated to us include: the stepper motors, FPGA system control board, the
motor control boards, and the Chameleon USB2.0 camera. The stepper motors, motor control boards, and the FPGA system control board are ``in-house" proprietary boards developed by BioFire Defense Systems.
The FPGA board embeds a Xilinx Spartan3 with a softcore Microblaze processor. The Chameleon USB2.0 cameras were donated to us by Point Grey Research. They a 1.3 megapixel camera with a Sony ICX445 CCD, 1/3", 3.75 micron sensor.

\begin{table*}[!ht]
\caption{Main component BOM}
\label{table:BOM}
\resizebox{\textwidth}{!}{\begin{tabular}{|l|c|c|c|c|}
\hline
\textbf{Part Description} & \textbf{Quantity} & \textbf{Vendor}     & \textbf{Vendor PN} & \textbf{Price/Unit (dollars)} \\ \hline
Stepper Motor             & 6                 & BioFire Defense       & NA                 & DONATED                \\ \hline
Pneumatic 12mmx25mm Double Action Thin Air Cylinder              & 6                 & Amico               & A12030500UX0057    & 7.86                \\ \hline
24V 2 Position 5 Way Pneumatic Solenoid Valve           & 6                 & Uxcell              & A11102700UX0130    & 10.31               \\ \hline
FPGA System Control Board      & 1                 &BioFire Defense        & NA                 & DONATED                \\ \hline
Motor Control Board       & 2                 & BioFire Defense       & NA                 & DONATED                \\ \hline
8 Channel 5V Relay Board               & 1                 & SainSmart           & 20-018-102         & 11.99               \\ \hline
Chameleon USB2.0 Camera                    & 2                 & Point Grey Research & CMLN-13S2C-CS      & DONATED                \\ \hline
\end{tabular}}
\end{table*}

\section{Summary}
This project is evidence of our team's ability to design a complex system containing software, electrical hardware, and mechanical hardware components. Project Herbert is a project that integrates various technologies and domains of engineering into one complete package. Working on this project has exposed us to a real-world application of system integration and, most importantly, teamwork. Project Herbert brought many challenges to our team, and we were able to overcome them with clever compromises. The image processing proved to be very difficult due to the lack of vision and poor lighting effects. We overcame this by creating a clever execution of moves that allowed us to capture all of the facelets using a single camera, as well as a unique color characterization that uses histogram calculations. We were unable to get robust and reliable switches for the mechanical actuations, and so we slowed down the actuations to ensure that any two adjacent arms would not collide with one another. Likewise, team scheduling proved to be another challenge for us. Half of our team works part-time. This made it difficult to find times to work on the project together. However, despite these challenges, we were able to implement the Rubik's cube solver as we had planned. We did not have enough time to make further optimizations to go for a Guinness World Record, but we are very satisfied to have a completely automated solver despite all of the compromises that we had to make. \section{Acknowledgements}
Our team would like to thank BioFire Defense LLC, Point Grey Research Inc., and Futura Industries for all the support and resources they have provided us. Your contributions are greatly appreciated.

\begin{figure}[!hb]
\begin{center}
\minipage{0.32\textwidth}
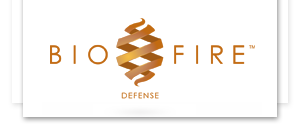
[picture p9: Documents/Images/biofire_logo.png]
  
  \label{fig:biofire_logo}
\endminipage\hfill
\minipage{0.32\textwidth}
  
  \label{fig:point_grey}
\endminipage\hfill
\minipage{0.32\textwidth}%
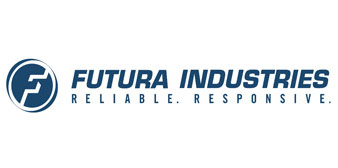
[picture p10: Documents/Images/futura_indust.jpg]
  
  \label{fig:futura_indst}
\endminipage
\label{fig:project_sponsors}
\end{center}
\end{figure}

BioFire Defense donated the various control boards and mechanical components needed for this project. They also gave us access to various prototyping tools including high precision 3D printers and laser cutters. A special thanks goes out to BioFire engineers Logan Taylor (Mechanical), Pat Riley (Electrical/Systems), Matt Murdock (Electrical), and David Nielsen (VP of Product Development). These individuals provided invaluable time and knowledge to our team.

We'd also like to thank Vladimir Tucakov of Point Grey Research. He provided our team with their Chameleon CMLN-13S2M-CS camera which we used for image acquisition.

We couldn't have put all these components together without a nice chassis to house them all. For this, we would like to thank Futura Industries. They helped us in the design and construction of the aluminum frame we used to house Herbert. Another special thanks goes out to Futura's Kenton Frandsen (Mechanical/Manufacturing Engineer) who assisted in the mechanical design of the mechanical arms and frame of our project.

% Insert the Bibliography
\printbibliography

\appendix
\section{Rubik's Cube Notation and Terminology}
\label{sec:Appendix A}
In order to solve a cube, it is standard to define the terminology and orientation layout used in Rubik's Cube theory and analysis. This section describes the basic notation that is used throughout this document.

\subsection{Faces}
A Rubik's Cube is composed of six faces: right (\textbf{R}), left (\textbf{L}), up (\textbf{U}), down (\textbf{D}), front (\textbf{F}), and back (\textbf{B}) (see Fig. \ref{fig:Cube Orientation}). The exact color of each face is relative to the orientation in which you are holding the cube. For example, if you align the blue face towards you then the blue face is defined as the front face. Each face can be rotated in two different directions: \textit{clockwise} or \textit{counter-clockwise}. These rotations are defined as the direction of rotation when looking directly at that face.

\begin{figure}[!hb]
\centering

\caption{Cube orientation}
\label{fig:Cube Orientation}
\end{figure}

\subsection{Fundamental Moves}
\label{sec:fundamental moves}
The most fundamental moves are 90-degree clock-wise rotations for each of the faces outlined above. These moves are outlined below \cite{BasicCubeNotation}:

\begin{itemize}

\item{\textbf{R}} - Indicates a 90-degree clockwise rotation of the right face such that the side on top rotates towards the back.
\item{\textbf{L}} - Indicates a 90-degree clockwise rotation of the left face such that the side on top rotates towards the front.
\item{\textbf{U}} - Indicates a 90-degree clockwise rotation of the upper face such that the side in front moves to the left.
\item{\textbf{D}} - Indicates a 90-degree clockwise rotation of the downward face such that the side in front moves to the right.
\item{\textbf{F}} - Indicates a 90-degree clockwise rotation of the front face such that the side on top moves to the right.
\item{\textbf{B}} - Indicates a 90-degree clockwise rotation of the back face such that the side on top moves to the left.
\end{itemize}

\subsection{Modifiers}
For each of the fundamental moves above, there are modifiers that can be appended to the move to change the rotation of the face. My example below uses \textbf{L} as the base move, but these modifiers can be applied to any of the fundamental moves.

\begin{itemize}
\item \textbf{L'} - Indicates a 90-degree counter-clockwise rotation of the left face such that the side on top rotates towards the back (opposite direction as that defined above).
\item \textbf{L2} - Indicates a 180-degree rotation of the left face (two rotations).
\end{itemize}

\subsection{Cubelets}
A cubelet refers to a particular piece on the cube. Cubelets are categorized based on their position. There are three types of cubelets: center cubelets, edge cubelets, and corner cubelets (see Fig. \ref{fig:cubelet_categories}). A center cubelet is unique. All other cubelets revolve around the center cubelets, they never move (go ahead, try and move the center piece). Edge cubelets connect two face pieces together at an edge. A corner cubelet connects three pieces together at the corner of the cube.

\begin{figure}[!hb]
\begin{center}
\minipage{0.32\textwidth}
  
  \label{fig:center_cubelets}
\endminipage\hfill
\minipage{0.32\textwidth}
  
  \label{fig:edge_cubelets}
\endminipage\hfill
\minipage{0.32\textwidth}%
  
  \label{fig:corner_cubelets}
\endminipage
\caption{Cubelet categories}
\label{fig:cubelet_categories}
\end{center}
\end{figure}

\end{document}
% end of document content

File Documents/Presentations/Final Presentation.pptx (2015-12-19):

## HERBERT Autonomous Rubik’s Cube Solver

Dylan Lytle
Li Lao
Matt Frandsen
Jon Whitaker

## What inspires you?

- CubeStormer1 & 3 – Fastest robot to solve a Rubik’s Cube (3.253s) [1].
- Zackary Gromko – Claims a new record on October 15, 2015 (2.39s) [2].

https://youtu.be/bEiQwmEe45s?t= (https://youtu.be/bEiQwmEe45s?t=13s)13s (https://youtu.be/bEiQwmEe45s?t=13s)

https://youtu.be/ (https://youtu.be/X0pFZG7j5cE)X0pFZG7j5cE (https://youtu.be/X0pFZG7j5cE)

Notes: Jon

## Introduction

GOAL: Create an autonomous robotic Rubik's Cube solver.
- Integrates various technologies
  - Video cameras, stepper motors, mechanical actuators, single-board computer, FPGA
- Possibly overtake Guinness World Record (3.253s at the time)
- Optimize mechanical and image processing operations while maintaining the precision needed to solve the cube.

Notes: Jon

## High level System Diagram

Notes: Jon

## OpenCV & Image Processing

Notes: Li

## OpenCV & Image Processing

Original Plan
- Two cameras, one for three of the six faces of the cube.
- Grayscale conversion – Convert RGB to pixel intensity for feature filtration [3].
- Canny edge detection - Identify the edges of the cube and the faces [4].
- Contour filtering - Identify cubelets on each face [5].

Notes: Li

## OpenCV & Image Processing

Final Implementation
- One camera
- Static mask

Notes: Li

## Opencv and Image PRocessing

- HSV conversion – Convert RGB to HSV [3].
- HSV characterization – Use pixel histogram and bin each facelet (square) [6].
- Histogram optimization

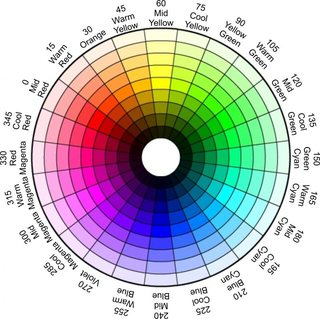
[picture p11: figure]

## Kcube & Solution Sequence

- Cubelets represented with an ASCII character
  - ‘W’, ‘R’, ‘B’, ‘G’, ‘O’, ‘Y’
- Kcube application used to generate the solution sequence [5].
  - Created by Greg Schmidt
  - Utilizes Kociemba’s algorithm
Microsoft Windows [ Version X.X. XXX ]
Copyright (c) 2015 Microsoft Corporation . All rights reserved .
c:> kcube L: GGWWOWBRB F: GWGBGYWBO U: YOOOWYROY D: ORGWYYYRB R: OGBBRYWRR B: YBROBGWGR

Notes: Jon

## Mechanical Actuators

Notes: Dylan

## Mechanical Actuators

- One arm for each face
  - Improvement over 4 arms solutions
- Each arm actuates, avoiding contact with the other arms

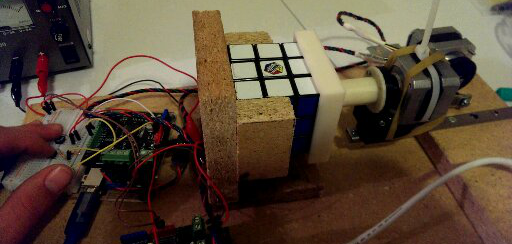
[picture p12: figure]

Original Ideas
  - Rotary → Linear motion
  - Linear actuator motor

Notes: Dylan

## Mechanical Actuators

Final Implementation
- Double action pneumatic air cylinder
  - High Speed
  - Affordable
  - Small footprint
- Controlled by solenoid valve and a relay board
- Simultaneous coaxial pair motion
- Approximately 40-60psi

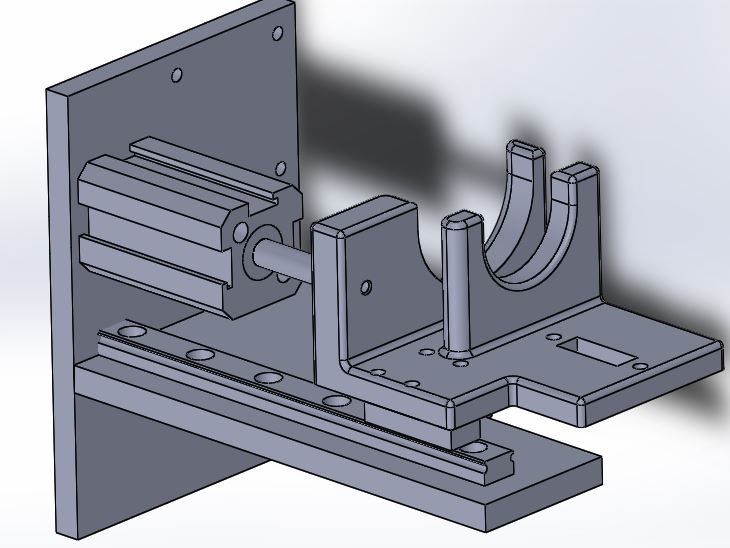
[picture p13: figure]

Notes: Dylan

## Electro-Mechanical Stepper Motors

## Electro-Mechanical Stepper Motors

- Each actuating arm has a stepper motor to rotate each face
- 90/180 degree rotations clockwise or counter-clockwise
- Controlled by an FPGA and proprietary motor control board
- Full steps, no micro-stepping
- Break sensor for 90 degree
alignment

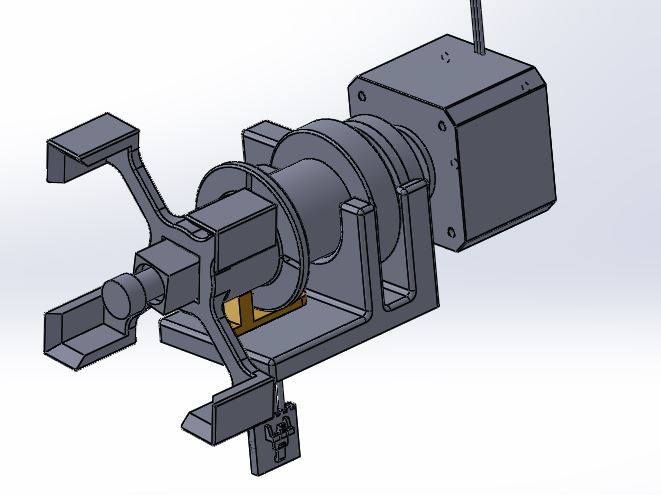
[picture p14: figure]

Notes: Matt

## Electro-Mechanical Stepper Motors

Progression of Arm Pieces

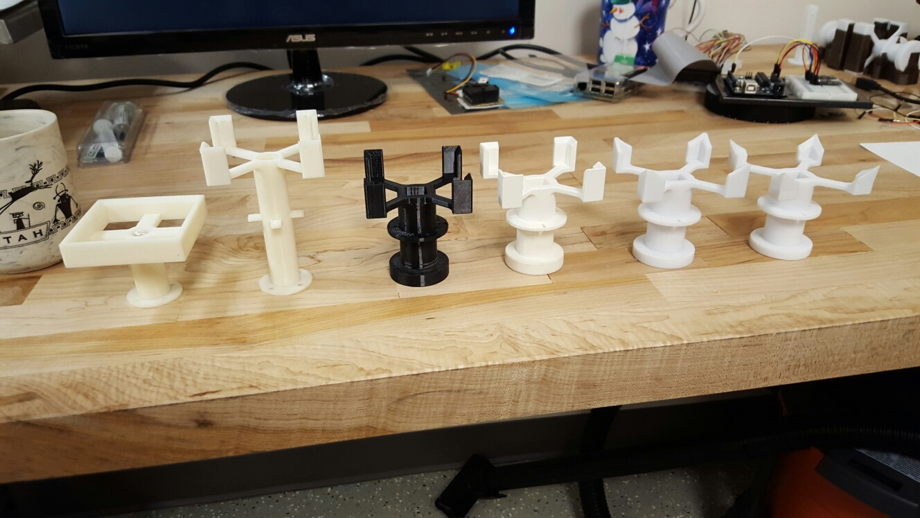
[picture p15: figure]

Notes: Matt

## Challenges

- Implementing & Synchronizing a system with 6 arm assemblies
- System integration
- Construction & Component acquisition
- Image processing
  - ROI issues
  - Color characterization (lighting)
- Team scheduling

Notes: Jon

## Summary

- Integrates various technologies and domains of engineering.
  - Computer and Electrical engineering combined with mechatronics and robotics
- Overcame many challenges
- Great application of system integration and teamwork.

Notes: Jon

## Acknowledgments

- Point Grey Research
- BioFire Defense
- Futura Industries


## REFERENCES

[1] Guinness World Records. Fastest robot to solve a Rubik's Cube [Online]. Available: http:// (http://www.guinnessworldrecords.com/world-records/fastest-robot-to-solve-a-rubiks-cub)www.guinnessworldrecords.com/world-records/fastest-robot-to-solve-a-rubiks-cub
[2] Guinness World Records. Robot created by American student solves a Rubik’s cube in just 2.39 seconds [Online]. Available: http://www.guinnessworldrecords.com/news/2015/11/robot-created-by-american-student-solves-a-rubiks-cube-in-just-2-39-seconds (http://www.guinnessworldrecords.com/news/2015/11/robot-created-by-american-student-solves-a-rubiks-cube-in-just-2-39-seconds)
[3] OpenCV Developers Team. Miscellaneous Image Transformations [Online].
Available: http:// (http://docs.opencv.org/modules/imgproc/doc/miscellaneous_transformations.html%23cvtcolor)docs.opencv.org/modules/imgproc/doc/miscellaneous_transformations.html#cvtcolor
[4] OpenCV Developers Team. Feature Detection [Online]. Available: http (http://docs.opencv.org/modules/imgproc/doc/feature_detection.html?highlight=canny%23canny)://docs.opencv.org/modules/imgproc/doc/feature_detection.html?highlight=canny#canny
[5] OpenCV Developers Team. Structural Analysis and Shape Descriptors [Online]. Available: http://docs.opencv.org/modules/imgproc/doc/structural_analysis_and_shape_descriptors.html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
[6] OpenCV Developers Team. Histograms in OpenCV [Online]. Available: http (http://opencv-python-tutroals.readthedocs.org/en/latest/py_tutorials/py_imgproc/py_histograms/py_histogram_begins/py_histogram_begins.html)://opencv-python-tutroals.readthedocs.org/en/latest/py_tutorials/py_imgproc/py_histograms/py_histogram_begins/py_histogram_begins.html (http://opencv-python-tutroals.readthedocs.org/en/latest/py_tutorials/py_imgproc/py_histograms/py_histogram_begins/py_histogram_begins.html)

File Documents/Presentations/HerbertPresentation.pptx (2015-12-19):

## HERBERT Autonomous Rubik’s Cube Solver

Dylan Lytle
Li Lao
Matt Frandsen
Jon Whitaker

## Background

- CubeStormer 3 – Fastest robot to solve a Rubik’s Cube (3.253s) [1].

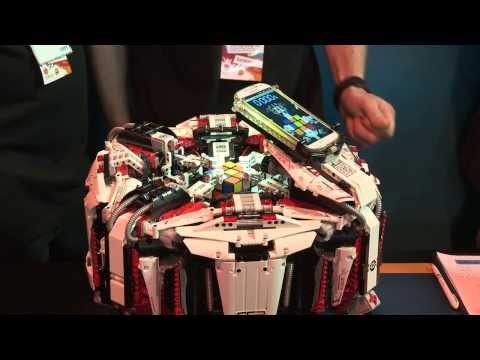
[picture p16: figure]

https://youtu.be/ (https://youtu.be/X0pFZG7j5cE)X0pFZG7j5cE (https://youtu.be/X0pFZG7j5cE)

## Introduction

GOAL: Create an autonomous robotic Rubik's Cube solver.
- Integrates various technologies
  - Video cameras, stepper motors, mechanical actuators, single-board computer, FPGA
- Possibly take Guinness World Record (3.253s)
- Optimize mechanical operations while maintaining the precision needed to rotate the cube.

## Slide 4

Cube Representation

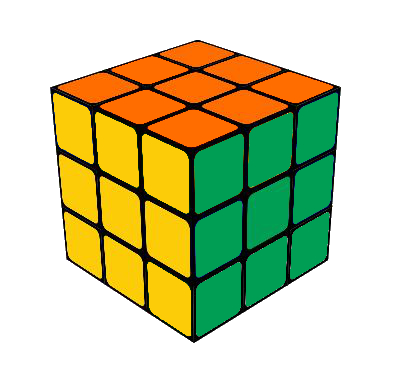
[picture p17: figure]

Face

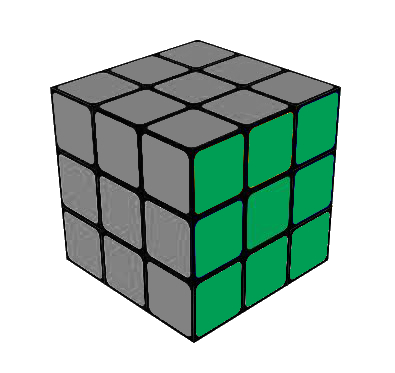
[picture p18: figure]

Corner

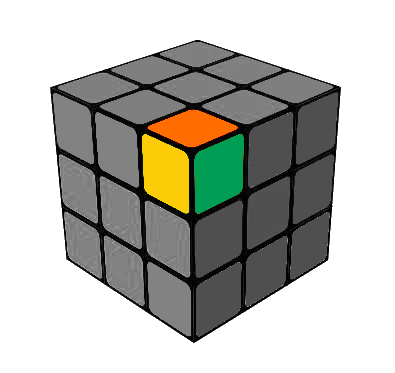
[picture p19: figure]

Cubies

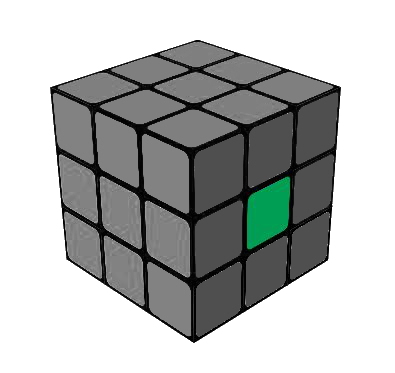
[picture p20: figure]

Cubelet

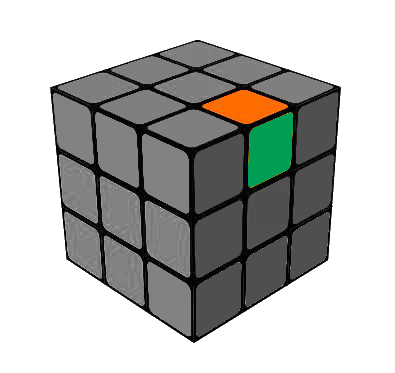
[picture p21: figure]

Edge

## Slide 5

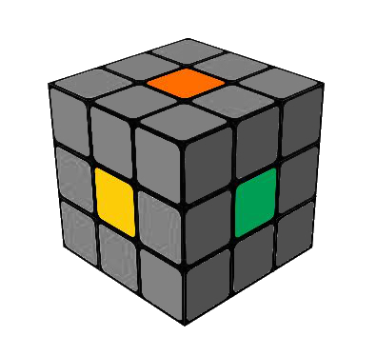
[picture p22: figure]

Middle Facelets Determine Face Color
(U = Orange, R = Green, F = Yellow, etc.)

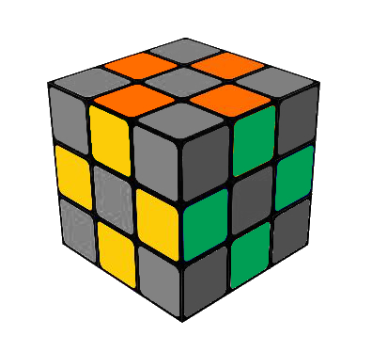
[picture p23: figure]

12 Edge Cubies

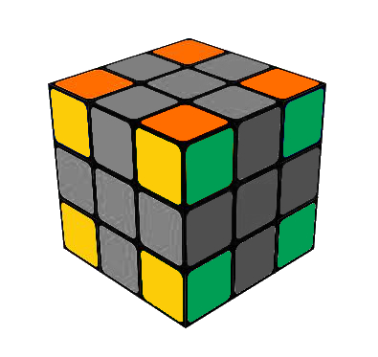
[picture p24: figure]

8 Corner Cubies

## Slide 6

R’
R Face Twisted Counterclockwise

F
F Face Twisted Clockwise


U2
U Face Twisted 180 Degrees

U

L

F

R

B

D


## High level System Diagram


## OpenCV & Image Processing

- Two cameras, one for three of the six faces of the cube.
- Grayscale conversion – Convert RGB to pixel intensity for feature filtration [2].
- Canny edge detection - Identify the edges of the cube and the faces [3].
- Contour filtering - Identify cubelets on each face [4].

## Kcube & Solution Sequence

- Cubelets represented with an ASCII character
  - ‘W’, ‘R’, ‘B’, ‘G’, ‘O’, ‘Y’
- Kcube application used to generate the solution sequence [5].
  - Created by Greg Schmidt
  - Utilizes Kociemba’s algorithm
Microsoft Windows [ Version X.X. XXX ]
Copyright (c) 2015 Microsoft Corporation . All rights reserved .
c:> kcube L: GGWWOWBRB F: GWGBGYWBO U: YOOOWYROY D: ORGWYYYRB R: OGBBRYWRR B: YBROBGWGR

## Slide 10


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

U

F

F2

Kociemba Two-Phase
Algorithm

Phase 1
- 43,252,003,274,489,856,000 possible starting orientations
- All 18 possible moves are used
- Uses pruning and symmetries
- 2,217,093,120 possible phase 1 solutions

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

Phase 1 Solution: F, U, F2, L2, U2, B2, L’, U, R2, F, B’ (11 moves)

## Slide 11


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

U

R2

Phase 2
- 2,217,093,120 possible starting orientations
- A subset of 10 moves are used
- Uses pruning and symmetries
- 1 possible phase 2 solution

Phase 2 Solution: U, R2, D’, R2, U’, F2, U, D, B2 (9 moves)

Final Solution: F, U, F2, L2, U2, B2, L’, U, R2, F, B’, U, R2, D’, R2, U’, F2, U, D, B2 (20 moves)

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

D

B2

## Mechanical Actuators

- One arm for each face
- Each arm must actuate, avoiding contact with the other arms
- Initial design ideas:
  - Rotary motion to linear motion
  - Linear actuator motor
- Solution: Double action pneumatic air cylinder
  - High Speed
  - Affordable
  - Small footprint
- Controlled by solenoid valve and a
relay board
- Simultaneous coaxial pair motion
- Approximately 80-100psi


## Electro-Mechanical Stepper Motors

- Each actuating arm will have a stepper motor to rotate each face
- 90/180 degree rotations clockwise or counter-clockwise
- Controlled by an FPGA and proprietary motor control board
- Full steps, no micro-stepping
- Break sensor for 90 degree
alignment.


## Summary

- Integrates various technologies and domains of engineering.
  - Computer and Electrical engineering combined with mechatronics and robotics
- Great application of system integration and teamwork.
- Mechanical components pose the greatest limitations.

## Acknowledgments

- Point Grey Research
- BioFire Defense
- Futura Industries


## REFERENCES

[1] Guinness World Records. Fastest robot to solve a Rubik's Cube [Online]. Available: http:// (http://www.guinnessworldrecords.com/world-records/fastest-robot-to-solve-a-rubiks-cub)www.guinnessworldrecords.com/world-records/fastest-robot-to-solve-a-rubiks-cub
[2] OpenCV Developers Team. Miscellaneous Image Transformations [Online].
Available: http:// (http://docs.opencv.org/modules/imgproc/doc/miscellaneous_transformations.html%23cvtcolor)docs.opencv.org/modules/imgproc/doc/miscellaneous_transformations.html#cvtcolor
[3] OpenCV Developers Team. Feature Detection [Online]. Available: http (http://docs.opencv.org/modules/imgproc/doc/feature_detection.html?highlight=canny%23canny)://docs.opencv.org/modules/imgproc/doc/feature_detection.html?highlight=canny#canny
[4] OpenCV Developers Team. Structural Analysis and Shape Descriptors [Online]. Available: http://docs.opencv.org/modules/imgproc/doc/structural_analysis_and_shape_descriptors.html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
[5] Herbert Kociemba. The Two-Phase Algorithm [Online]. Available: http://kociemba.org/cube.htm

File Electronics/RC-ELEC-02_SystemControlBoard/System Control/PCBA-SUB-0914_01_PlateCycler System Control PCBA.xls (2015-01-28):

 |  | Drawing Title: | Number: |  | Revision: | Filename:
 |  | PlateCycler System Control Schematic | PCBS-SCM-0914 |  | 01 | PCBS-SCM-0914_01_PlateCycler System Control Schematic.pdf
 |  | PlateCycler System Control Layout | PCBS-GEN-0914 |  | 01 | PCBS-GEN-0914_01_PlateCycler System Control Layout.xls
 |  | PlateCycler System Control BOM | PCBS-BOM-0914 |  | 01 | PCBS-BOM-0914_01_PlateCycler System Control BOM.xls
 |  | PlateCycler System Control Manufacturing Notes | PCBS-MFG-0914 |  | 01 | PCBS-MFG-0914_01_PlateCycler System Control Manufacturing Notes.xls
 |  | Incoming Inspection Methodology: | Abbreviated
 |  | Specifications: | Criteria: |  |  | Firmware Associated with this Assembly: |  | Programmed?
 |  | Subassembly Part Number | ▲PCBA-SUB-0914-01 |  |  | TBD |  | TBD
 |  | PCB Part Number | ▲PCBS-GEN-0914-01
 |  | Flame Rating | ▲94V-0 or better
 |  | Optical Inspection Stamp | ▲Vendor-specific Indicator
 |  |  |  | "▲" Mark indicates a critical inspection criteria that will be verified during incoming inspection
REVISIONS |  |  | TITLE: | PlateCycler System Control PCBA
REV | DATE | DESCRIPTION | ASSEMBLY (PART) NUMBER:
01 | 2010-04-05 | Initial release | PCBA-SUB-0914
 |  |  | PROJECT: | PlateCycler
 |  |  |  |  |  | 390 Wakara Way - Salt Lake City - UT 84108 (801) 736-6354 - www.idahotech.com
 |  |  |  | DATE | SIGNATURE
 |  |  |  |  |  | Proprietary and Confidential | SIZE | REV
 |  |  | DESIGNER |  |  | THE INFORMATION CONTAIN IN THIS DRAWING IS THE SOLE PROPERTY OF IDAHO TECHNOLOGY. ANY REPRODUCTION IN PART OR AS A WHOLE WITHOUT THE WRITTEN PERMISSION OF IDAHO TECHNOLOGY IS PROHIBITED. | A | 01
 |  |  | CHK'D BY
 |  |  | MANAGER |  |  |  | SHEET 1 OF 1
 |  |  | FILENAME: PCBA-SUB-0914_01_PlateCycler System Control PCBA.xls

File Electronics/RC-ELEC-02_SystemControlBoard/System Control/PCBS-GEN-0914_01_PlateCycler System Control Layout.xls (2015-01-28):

 |  | Description |  |  |  | Filename
 |  | PCB Layout Document |  |  |  | System Control.PCBDOC
 |  | FOLLOWING FILES ZIPPED FOR PCB MANUFACTURING** |  |  |  | System Control Gerber Files.zip
 |  | Pick and Place File |  |  |  | Pick Place for System Control.txt
 |  | Aperture Data |  |  |  | System Control.apr
 |  | NC Drill Binary |  |  |  | System Control.DRL
 |  | NC Drill Report |  |  |  | System Control.DRR
 |  | EXTREP File - description of Gerber File Extensions |  |  |  | System Control.EXTREP
 |  | Layer 3 Gerber Data |  |  |  | System Control.G1
 |  | Layer 4 Gerber Data |  |  |  | System Control.G2
 |  | Layer 6 Gerber Data |  |  |  | System Control.G3
 |  | Layer 7 Gerber Data |  |  |  | System Control.G4
 |  | Layer 9 Gerber Data |  |  |  | System Control.G5
 |  | Layer 10 Gerber Data |  |  |  | System Control.G6
 |  | GND Layer 2 Gerber Data |  |  |  | System Control.GP1
 |  | 3.3V Layer 5 Gerber Data |  |  |  | System Control.GP2
 |  | 2.5V Layer 8 Gerber Data |  |  |  | System Control.GP3
 |  | GND Layer 11 Gerber Data |  |  |  | System Control.GP4
 |  | Bottom Overlay Gerber Data |  |  |  | System Control.GBO
 |  | Bottom Paste Mask Gerber Data |  |  |  | System Control.GBP
 |  | Bottom Pad Master Gerber Data |  |  |  | System Control.GPB
 |  | Top Pad Master Gerber Data |  |  |  | System Control.GPT
 |  | Bottom Layer Gerber Data |  |  |  | System Control.GBL
 |  | Bottom Solder Mask Gerber Data |  |  |  | System Control.GBS
 |  | Drill Drawing Layer Pair Gerber Data |  |  |  | System Control.GD1
 |  | Drill Guide Layer Pair Gerber Data |  |  |  | System Control.GG1
 |  | Keepout Layer Gerber Data |  |  |  | System Control.GKO
 |  | Internal Plane Layer 1 Gerber Data |  |  |  | System Control.GP1
 |  | Internal Plane Layer 2 Gerber Data |  |  |  | System Control.GP2
 |  | Top Layer Gerber Data |  |  |  | System Control.GTL
 |  | Top Overlay Gerber Data |  |  |  | System Control.GTO
 |  | Top Paste Mask Gerber Data |  |  |  | System Control.GTP
 |  | Top Solder Mask Gerber Data |  |  |  | System Control.GTS
 |  | NC Drill TXT File |  |  |  | System Control.TXT
 |  | **Send ZIP file to vendor when initial PCB fabrication is required
REVISIONS |  |  | TITLE: | PlateCycler System Control Layout
REV | DATE | DESCRIPTION | PART NUMBER:
01 | 2010-04-05 | Initial release | PCBS-GEN-0914
 |  |  | PROJECT: | PlateCycler
 |  |  |  |  |  | 390 Wakara Way - Salt Lake City - UT 84108 (801) 736-6354 - www.idahotech.com
 |  |  |  | DATE | SIGNATURE
 |  |  |  |  |  | Proprietary and Confidential | SIZE | REV
 |  |  | DESIGNER |  |  | THE INFORMATION CONTAIN IN THIS DRAWING IS THE SOLE PROPERTY OF IDAHO TECHNOLOGY. ANY REPRODUCTION IN PART OR AS A WHOLE WITHOUT THE WRITTEN PERMISSION OF IDAHO TECHNOLOGY IS PROHIBITED. | A | 01
 |  |  | CHK'D BY
 |  |  | MANAGER |  |  |  | SHEET 1 OF 1
 |  |  | FILENAME: PCBS-GEN-0914 PlateCycler System Control Layout.xls

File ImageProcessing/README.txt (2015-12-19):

The "ImageProcessing" directory contains all the source code and files used in the
image processing and interfacing with the FPGA system.

This README outlines what each file is being used for in the overall system.

--------
main.py
--------
main.py contains our main server side program that performs capturing cube state,
image processing, finding solve sequence, and send over solution sequence to FPGA.

Example: python main.py --id 0 

 --id               - The device ID for top Camera.
 --disableOptimized - Disables image processing optimization
 --sequenceMode     - Execute all solving move sequence in one ExecuteCommand 
 --debug            - Enable debugging prints
 --t_thresh         - Amount of time to wait for KCUBE to find optimized solution
 --port             - The COM port which the FPGA is plugged into.

----------------
commInterface.py
----------------
commInterface.py contains all the code used to communicate serially with the FPGA.
commInterface.py is used by main.py and should be in the same directory. Performs
CRC32 calculations and connects to the FPGA serially.

---------------
kcube directory
---------------
Contains 3rd party code provided by Kociemba. The source of this file is can be found
in our document.

----------------------
Additional *.txt files
----------------------
Contains all the static polygon mask for each of the facelet and is used by
main.py for image capturing.

----------------------------
HerbertCommInterfaceGUI.py/ui
----------------------------
Used to manually communicate serially with the FPGA. It is used for debugging one
the server side with a GUI.

---------------
test_points.py
---------------
test_points.py is used as a helper python script to test each of the masks defined
for each facelet. Through this script, we can quickly visualize if all the mask 
are correctly aligned.

Example: python test_points.py -p mask_file.txt -d image_directory

---------------
cube_capture.py
---------------
cube_capture.py contains prototype code for dynamic cube state detection. 

---------
main.cpp
---------
main.cpp contains old image processing code in C++ before we had to port to python.

---------
*.bmp
---------
Some example images we taken during a solve sequence


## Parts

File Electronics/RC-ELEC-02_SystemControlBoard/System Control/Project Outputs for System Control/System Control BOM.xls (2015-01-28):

 | BILL OF MATERIALS FOR ELECTRONICS |  |  |  |  |  |  |  |  | Form #: IT 403G
 | Idaho Technology Inc. |  |  |  |  |  |  |  |  | Rev.: 01
 |  |  |  |  |  |  |  |  |  | Date Effective: 3/18/05
Approvals
Development Manager |  |  | Date | Production Manager |  |  | Date | QA |  | Date
Part #: |  |  | Title: |  |  |  |  |  | Revision:
Project: |  |  | Master Assembly Number: |  |  |  |  |  | Effective Date:
Quantity | Designator | Comment | Description |  | Manufacturer | Manufacturer P/N | Vendor | Vendor P/N | Notes
12 | C1, C2, C3, C4, C8, C9, C11, C12, C22, C23, C37, C38 | 10uF 25V | SMD Tantalum Capacitors 10uF 25V 20% L ESR |  | AVX | TPSC106M025R0500 | Mouser | 581-TPSC106M025R0500
37 | C5, C10, C18, C21, C32, C34, C42, C44, C47, C48, C53, C57, C64, C65, C69, C79, C100, C170, C171, C183, C205, C208, C209, C211, C213, C215, C226, C227, C231, C232, C234, C235, C236, C237, C238, C246, C248 | 0.1uF 50V | CAP CER .10UF 50V X7R 0603 |  | Taiyo Yuden | UMK107B7104KA-T | Digikey | 587-1243-1-ND
9 | C6, C13, C14, C55, C56, C63, C80, C81, C253 | 1uF 25V | CAP 1UF 25V CERAMIC 0603 X5S |  | Panasonic | ECJ-1V41E105M | Digikey | PCC2354CT-ND
1 | C7 | 0.1uF 50V | CAP .1UF 50V CERM CHIP 1206 X7R |  | Panasonic | ECJ-3VB1H104K | Digikey | PCC104BCT-ND
15 | C15, C36, C43, C45, C46, C49, C50, C59, C104, C112, C115, C163, C175, C247, C251 | 4.7uF 10V | CAP CER 4.7UF 10V Y5V 0603 |  | Murata | GRM188F51A475ZE20D | Digikey | 490-3302-1-ND
1 | C17 | 0.033uF 50V | CAP .033UF 50V CERAMIC X7R 0603 |  | Panasonic | ECJ-1VB1H333K | Digikey | PCC2284CT-ND | Obsolete Part - Non Stock
1 | C25 | 100uF 25V | CAPACITOR TANT 100UF 25V 20% SMD |  | Kemet | T510E107M025AT E050 | Digikey | 399-3989-1-ND
6 | C35, C54, C102, C105, C124, C172 | 470uF 10V | CAP TANT LOESR 470UF 10V 10% SMD |  | AVX Corporation | TPSV477K010R0060 | Digikey | 478-4162-1-ND
33 | C58, C60, C61, C62, C66, C67, C68, C76, C77, C78, C85, C86, C87, C88, C180, C182, C185, C187, C210, C212, C214, C216, C225, C228, C229, C230, C233, C240, C241, C242, C243, C244, C245 | 0.01uF 50V | CAP 10000PF 50V CERM X7R 0603 |  | Panasonic | ECJ-1VB1H103K | Digikey | PCC1784CT-ND | Obsolete Part - Non Stock
15 | C106, C108, C110, C116, C123, C134, C146, C153, C155, C156, C168, C169, C179, C181, C186 | 1uF 10V | CAP CER 1.0UF 10V X5R 10% 0402 |  | AVX Corporation | 0402ZD105KAT2A | Digikey | 478-4596-1-ND
45 | C107, C109, C113, C117, C118, C119, C120, C121, C122, C125, C126, C127, C129, C130, C131, C132, C133, C135, C136, C137, C138, C139, C140, C141, C142, C143, C145, C147, C148, C149, C150, C151, C152, C154, C157, C158, C159, C160, C161, C164, C165, C167, C173, C174, C178 | 0.01uF 25V | CAP .01UF 25V CERAMIC X7R 0402 |  | Panasonic | ECJ-0EB1E103K | Digikey | PCC2270CT-ND | Obsolete Part - Non Stock
11 | D1, D2, D4, D5, D8, D9, D12, D13, D14, D15, D16 | RED | LED 635NM RED WTR CLR 1206 SMD |  | Lumex | SML-LX1206IC-TR | Digikey | 67-1356-1-ND
1 | D3 | MBRB2535CTLT4G | On Semi Switchmode Power Rectifier |  | On Semiconductor | MBRB2535CTLT4G | Digikey | MBRB2535CTLT4GOSCT-ND
1 | D6 | BLUE | LED INGAN/SIC U-BLUE CLR 1206SMD |  | Lumex | SML-LX1206USBC-TR | Digikey | 67-1701-1-ND
1 | DISP1 | Header 16X1 | CONN SOCKET STRIP LOPRO 16 PIN |  | MILL-MAX CORP | 801-43-016-10-012000 | Digikey | ED6516-ND
1 | F3 | 3A | FUSEBLOCK W/3A FUSE SMD FAST |  | Littelfuse Inc | 0154003.DR | Digikey | F1226CT-ND
2 | J1, J8 | Header 5X2 | CONN HEADER 10 POS STRGHT GOLD |  | 3M/ESD | N2510-6002RB | Digikey | MHC10K-ND
1 | J2 | Header 7X2 | CONN HEADER 14POS 2MM PCB TIN |  | Hirose | DF11-14DP-2DSA(24) | Digikey | H10234-ND
2 | J3, J5 | Header 5X2 | CONN HEADER 10POS 2MM PCB TIN |  | HIROSE | DF11-10DP-2DSA(24) | Digikey | H10232-ND
2 | J4, J12 | Header 17X2 | CONN HEADER LOPRO STR .100 34POS |  | Tyco | 1-1761608-1 | Digikey | A31188-ND
1 | J6 | Header 6X2 | CONN HEADER 12POS 2MM PCB TIN |  | HIROSE | DF11-12DP-2DSA(24) | Digikey | H10233-ND
2 | J7, J13 | Header 13X2 | CONN HEADER LOPRO STR .100 26POS |  | Tyco | 1761608-9 | Digikey | A31187-ND
1 | J9 | Header 6X2 | CONN HEADER 12POS .100" STR TIN |  | MOLEX | 90131-0126 | Digikey | WM8124-ND
1 | J10 | Header 4X2 | CONN HEADER 8POS 2MM PCB TIN |  | HIROSE | DF11-8DP-2DSA(24) | Digikey | H10231-ND
1 | J11 | Header 5X1 | CONN HEADER 5POS .100 VERT GOLD |  | Molex | 70543-0004 | Digikey | WM4803-ND
1 | J14 | Header 7X2 | CONN HEADER 14POS 2MM VERT GOLD |  | Molex | 87831-1420 | Digikey | WM17469-ND
1 | L1 | 2.2uH | INDUCTOR POWER 2.2UH 3.25A SMD |  | Vishay/Dale | IHLP1616BZER2R2M11 | Digikey | 541-1050-1-ND
8 | LD0, LD1, LD2, LD3, LD4, LD5, LD6, LD7 | LED | LED 565NM GRN DIFF 0603 SMD |  | Lumex Opto/Components Inc | SML-LX0603GW-TR | Digikey | 67-1549-1-ND
1 | Q1 | FDS6961A | MOSFET N-CH DUAL 30V 3.5A 8SOIC |  | Fairchild Semiconductor | FDS6961A | Digikey | FDS6961ACT-ND
9 | Q2, Q3, Q4, Q5, Q6, Q7, Q9, Q10, Q11 | NDS355 | MOSFET N-CH 30V 1.6A SOT-23 |  | Fairchild Semiconductor | NDS355N | Digikey | NDS355NCT-ND
1 | R1 | 100k 0.1% | RES 100K OHM 1/10W .1% 0805 SMD |  | Panasonic | ERA-6YEB104V | Digikey | P100KZCT-ND
17 | R2, R3, R4, R14, R19, R23, R33, R38, R39, R42, R73, R74, R99, R100, R174, R175, R176 | 1K 5% | RES 1.0K OHM 1/10W 5% 0603 SMD |  | Panasonic, PANASONIC - ECG | ERJ-3GEYJ102V | Digikey | P1.0KGCT-ND
30 | R5, R11, R12, R13, R15, R17, R21, R22, R24, R29, R31, R37, R40, R41, R47, R48, R49, R50, R146, R147, R150, R152, R153, R154, R155, R156, R163, R165, R183, R275 | 10K 5% | RES 10K OHM 1/10W 5% 0603 SMD |  | Panasonic | ERJ-3GEYJ103V | Digikey | P10KGCT-ND
1 | R6 | 5.11K 1% | RES 5.11K OHM 1/10W 1% 0603 SMD |  | Panasonic | ERJ-3EKF5111V | Digikey | P5.11KHCT-ND
1 | R7 | 750 5% | RES 750 OHM 1/10W 5% 0603 SMD |  | Panasonic | ERJ-3GEYJ751V | Digikey | P750GCT-ND
4 | R9, R27, R180, R294 | 0 | RES ZERO OHM 1/10W 5% 0603 SMD |  | Panasonic | ERJ-3GEY0R00V | Digikey | P0.0GCT-ND
2 | R10, R129 | 100 1% | RES 100 OHM 1/10W 1% 0805 SMD |  | Panasonic | ERJ-6ENF1000V | Digikey | P100CCT-ND
6 | R16, R158, R167, R170, R172, R178 | 4.7K 5% | RES 4.7K OHM 1/10W 5% 0603 SMD |  | Panasonic | ERJ-3GEYJ472V | Digikey | P4.7KGCT-ND
8 | R18, R28, R34, R36, R43, R44, R45, R46 | 270 5% | RES 270 OHM 1/10W 5% 0603 SMD |  | Panasonic | ERJ-3GEYJ271V | Digikey | P270GCT-ND
1 | R20 | 6.8K 1% | RES 6.80K OHM 1/10W 1% 0603 SMD |  | Panasonic | ERJ-3EKF6801V | Digikey | P6.80KHCT-ND
1 | R25 | 30.9K 1% | RES 30.9K OHM 1/10W 1% 0603 SMD |  | Panasonic | ERJ-3EKF3092V | Digikey | P30.9KHCT-ND
2 | R32, R35 | 33 5% | RES 33 OHM 1/10W 5% 0603 SMD |  | Panasonic | ERJ-3GEYJ330V | Digikey | P33GCT-ND
64 | R51, R52, R53, R54, R56, R58, R59, R60, R61, R62, R63, R64, R66, R68, R69, R70, R71, R72, R80, R81, R90, R92, R108, R110, R111, R117, R118, R119, R120, R121, R122, R123, R168, R192, R193, R195, R196, R198, R201, R202, R203, R205, R206, R207, R208, R210, R213, R222, R225, R228, R229, R232, R236, R239, R240, R266, R267, R268, R273, R274, R276, R277, R279, R282 | 60.4 1% | RES 60.4 OHM 1/16W 1% 0402 SMD |  | Panasonic | ERJ-2RKF60R4X | Digikey | P60.4LCT-ND
45 | R55, R57, R65, R67, R76, R77, R78, R79, R82, R83, R84, R85, R86, R87, R88, R89, R91, R93, R94, R95, R96, R97, R164, R194, R197, R199, R200, R204, R209, R211, R212, R221, R223, R224, R226, R227, R230, R231, R233, R234, R235, R237, R238, R241, R242 | 24 1% | RES 24.0 OHM 1/16W 1% 0402 SMD |  | Panasonic | ERJ-2RKF24R0X | Digikey | P24.0LCT-ND
4 | R75, R98, R101, R116 | 120 1% | RES 120 OHM 1/10W 1% 0603 SMD |  | PANASONIC - ECG | ERJ-3EKF1200V | Digikey | P120HCT-ND
25 | R102, R103, R104, R105, R106, R107, R109, R112, R113, R114, R115, R260, R261, R262, R263, R264, R265, R269, R278, R280, R281, R284, R286, R289, R290 | 33 1% | RES 33.0 OHM 1/16W 1% 0402 SMD |  | Panasonic | ERJ-2RKF33R0X | Digikey | P33.0LCT-ND
4 | R157, R160, R166, R171 | 49.9 1% | RES 49.9 OHM 1/10W 1% 0603 SMD |  | Panasonic | ERJ-3EKF49R9V | Digikey | P49.9HCT-ND
2 | R285, R287 | 100 0.5% | RES 100 OHM 1/16W .5% 0603 SMD |  | Susumu | RR0816P-101-D | Digikey | RR08P100DCT-ND
2 | S1, S3 | SW-PB | SWITCH KEY 4MM SQ SMD GULL WING |  | Bourns | 7914G-1-000E | Digikey | 7914G-000ECT-ND
2 | S2, S4 | SW-DIP4 | SWITCH DIP 4POS TOP SLIDE SMT |  | CTS Corporation Electro Components | 204-4ST | Digikey | CT2044ST-ND
15 | TP1, TP2, TP3, TP4, TP6, TP7, TP8, TP9, TP10, TP11, TP12, TP13, TP14, TP15, TP16 | TEST POINT | TEST POINT PC MINI .040"D RED |  | Keystone Electronics | 5000 | Digikey | 5000K-ND
1 | TP5 | TEST POINT | TEST POINT PC MINI .040"D BLACK |  | Keystone Electronics | 5001 | Digikey | 5001K-ND
1 | U1 | LT1963AEST-3.3 | IC REG LDO LN 1.5A 3.3V SOT-223 |  | Linear Technology | LT1963AEST-3.3#PBF | Digikey | LT1963AEST-3.3#PBF-ND
2 | U2, U12 | AT45DB161D | Flash Mem Serial-SPI 2.7V to 3.6V 16M-Bit 6ns 8-Pin SOIC |  | Atmel | AT45DB161D-SU | Digikey | AT45DB161D-SU-ND
1 | U3 | LT1963AEST-2.5 | IC REG LDO LN 1.5A 2.5V SOT223-3 |  | Linear Technology | LT1963AEST-2.5#PBF | Digikey | LT1963AEST-2.5#PBF-ND
2 | U4, U23 | MAX3221/SO | IC DRVR/RCVR RS-232 1-CH 16TSSOP |  | Maxim | MAX3221CPWR | Digikey | 296-9594-1-ND | Recommended Sub 296-9596-1-ND
1 | U5 | TPS51116PWP | Controllers - DC/DC DDR2 SWITCHER AND LDO |  | Texas Instruments | TPS51116PWP | Mouser | 595-TPS51116PWP
1 | U7 | TPS3307-25DGNR | IC 3.3/2.5V/ADJ TPL MONIT 8-MSOP |  | Texas Instruments | TPS3307-25DGNR | Digikey | 296-3313-1-ND
1 | U8 | AP1122EG-13 | IC REG LDO 1.0A POS SOT223 |  | Diodes Inc | AP1122EG-13 | Digikey | AP1122EGDICT-ND
1 | U9 | TPS3808G12DBVR | IC VOLT SUPERVISOR 1.2V SOT23-6 |  | Texas Instruments | TPS3808G12DBVR | Digikey | 296-17190-1-ND
1 | U10 | TPS3828-50QDBVRQ1 | IC 4.55V SUPPLY MONITOR SOT23-5 |  | Texas Instrument | TPS3828-50QDBVRQ1 | Digikey | 296-15659-1-ND
1 | U11 | XC3S1400A-4FGG676C | IC, SPARTAN-3A, FPGA, 1400K, 656FBGA |  | Xilinx Inc | XC3S1400A-4FGG676C | Digikey | 122-1551-ND
1 | U13 | Quad Opto-isolator | IC, OPTOCOUPLER, QUAD, BIDIR, 16-SOIC |  | AVAGO TECHNOLOGIES | ACSL-6420-00TE | Digikey | 516-1733-5-ND
2 | U21, U22 | DDR2 256MB | IC DDR2 SDRAM 256MB 84-FBGA |  | Micron Technology Inc | MT47H16M16BG-3:B TR | Digikey | 557-1046-1-ND
1 | U26 | SN74AHC1G08 | IC SGL 2IN POS-AND GATE SOT23-5 |  | Texas Instruments | SN74AHC1G08DBVR | Digikey | 296-1091-1-ND
4 | W1, W2, W3, W4 | Jumper | CONN HEADER 2POS .100" STR TIN |  | Molex | 90120-0122 | Digikey | WM8072-ND
1 | Y1 | 125 MHz | OSC 125.0000 MHZ 3.3V HCMOS SMT |  | FOX Electronics | FXO-HC735-125MHZ | Digikey | 631-1138-1-ND

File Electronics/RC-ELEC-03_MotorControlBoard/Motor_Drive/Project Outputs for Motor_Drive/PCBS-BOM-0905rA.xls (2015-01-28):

 | BILL OF MATERIALS FOR ELECTRONICS |  |  |  |  |  |  |  |  |  | Form #: IT 403G
 | Idaho Technology Inc. |  |  |  |  |  |  |  |  |  | Rev.: 01
 |  |  |  |  |  |  |  |  |  |  | Date Effective: 3/18/05
Approvals
Development Manager |  |  | Date | Production Manager |  |  | Date | QA |  |  | Date
Part #: | PCBS-BOM-0905 |  | Title: | Motor Drive Board |  |  |  |  | Revision: | A
Project: | Plate Cycler |  | Master Assembly Number: |  | PCBA-SUB-0905 |  |  |  | Effective Date:
LINE | QUANTITY | REFERENCE DESIGNATOR | DESCRIPTION | MANUFACTURER | MFG. PART NUMBER | VENDOR | VENDOR PART NUMBER | IT PART NUMBER | NOTES
1 | 4 | C1, C2, C33, C34 | CAPACITOR TANT 100UF 25V 20% SMD | Kemet | T510E107M025AT E050 | DIGIKEY | 399-3989-1-ND | N/A
2 | 8 | C3, C4, C5, C6, C35, C36, C37, C38 | CAP 56UF 50V ELECT FC RADIAL | PANASONIC | EEU-FC1H560 | DIGIKEY | P10322-ND | N/A
3 | 25 | C7, C8, C9, C10, C11, C12, C19, C20, C25, C27, C31, C39, C40, C41, C42, C43, C44, C52, C53, C58, C59, C60, C61, C62, C63, C64 | CAP CER .10UF 50V X5R 0603 | Taiyo Yuden | UMK107B7104KA-T | DIGIKEY | 587-1243-1-ND | N/A
4 | 12 | C13, C14, C15, C16, C17, C18, C46, C47, C48, C49, C50, C51 | CAP CER .22UF 50V Y5V 0603 | Murata Electronics North America | GRM188F51H224ZA01D | DIGIKEY | 490-1569-1-ND | N/A
5 | 8 | C21, C22, C23, C24, C54, C55, C56, C57 | CAP 1000PF 50V CERAMIC X7R 0603 | Panasonic | ECJ-1VB1H102K | DIGIKEY | PCC1772CT-ND | N/A
6 | 2 | C26, C28 | CAP CER 1.0UF 10V X5R 10% 0603 | TDK Corporation | C1608X5R1A105K | DIGIKEY | 445-1321-1-ND | N/A
7 | 4 | J12, J13, J14, J15 | Mounting Holes |  |  |  |  | N/A | DO NOT POPULATE
8 | 1 | C29 | CAP .1UF 50V CERM CHIP 1206 X7R | PANASONIC | ECJ-3VB1H104K | DIGIKEY | PCC104BCT-ND | N/A
9 | 1 | C30 | CAP TANTALUM 10UF 50V 20% SMD | KEMET | B45196H7106M509 | DIGIKEY | 495-2288-1-ND | N/A
10 | 1 | C32 | CAP CER .33UF 50V X7R 0805 | MURATA ELECTRONICS | GRM219R71H334KA88D | DIGIKEY | 490-3327-1-ND | N/A
11 | 1 | C45 | CAP 560UF 50V ELECT FC RADIAL | Panasonic | EEU-FC1H561 | DIGIKEY | P11261-ND | N/A
12 | 1 | D1 | DIODE SUPER FAST REC 2A 100V SMB | Diodes Inc. | ES2B-13-F | DIGIKEY | ES2B-FDICT-ND | N/A
13 | 1 | D2 | LED 565NM GRN DIFF 0603 SMD | Lumex Opto/Components Inc | SML-LX0603GW-TR | DIGIKEY | 67-1549-1-ND | N/A
14 | 1 | F1 | FUSEBLOCK W/.375A FUSE SMD FST | Littelfuse Inc | 0154.375DR | DIGIKEY | F3150CT-ND | N/A
15 | 1 | F2 | FUSEBLOCK W/2A FUSE SMD FAST | Littelfuse Inc | 0154002.DR | DIGIKEY | F1224CT-ND | N/A
16 | 4 | J1, J2, J4, J5 | CONN HEADER 4POS .100 VERT GOLD | Molex/Waldom Electronics Corp | 70543-0003 | DIGIKEY | WM4802-ND | N/A
17 | 1 | J3 | CONN HEADER 3POS .100 VERT GOLD | MOLEX | 70543-0002 | DIGIKEY | WM4801-ND | N/A
18 | 6 | J6, J7, J8, J9, J10, J11 | CONN HEADER 5POS .100 VERT GOLD | Molex | 70543-0004 | DIGIKEY | WM4803-ND | N/A
19 | 1 | P1 | CONN HEADER 12POS 2MM PCB TIN | HIROSE | DF11-12DP-2DSA(24) | DIGIKEY | H10233-ND | N/A
20 | 20 | R1, R2, R4, R5, R11, R12, R13, R14, R37, R38, R40, R41, R47, R48, R49, R50, R65, R66, R67, R68 | RES ZERO OHM 1/10W 5% 0603 SMD | ROHM SEMICONDUCTOR | MCR03EZPJ000 | DIGIKEY | RHM0.0GCT-ND | N/A | DO NOT POPULATE
21 | 17 | R3, R6, R7, R9, R24, R25, R27, R28, R33, R34, R35, R39, R42, R43, R45, R72, R74 | RES 1.00K OHM 1/10W 1% 0603 SMD | PANASONIC - ECG | ERJ-3EKF1001V | DIGIKEY | P1.00KHCT-ND | N/A
22 | 7 | R8, R10, R44, R46, R69, R70, R71 | RES 10K OHM 1/10W 5% 0603 SMD | Panasonic | ERJ-3GEYJ103V | DIGIKEY | P10KGCT-ND | N/A
23 | 8 | R15, R16, R17, R18, R51, R52, R53, R54 | RES 12.7K OHM 1/10W 1% 0603 SMD | Panasonic | ERJ-3EKF1272V | DIGIKEY | P12.7KHCT-ND | N/A
24 | 8 | R19, R20, R21, R22, R55, R56, R57, R58 | RES .56 OHM 1W 1% 2512 SMD | Panasonic | ERJ-1TRQFR56U | DIGIKEY | PT.56YCT-ND | N/A
25 | 9 | R23, R26, R29, R30, R31, R32, R36, R73, R75 | RES 237 OHM 1/10W 1% 0603 SMD | PANASONIC - ECG | ERJ-3EKF2370V | DIGIKEY | P237HCT-ND | N/A
26 | 6 | R59, R60, R61, R62, R63, R64 | RES 270 OHM 1/10W 5% 0603 SMD | Panasonic | ERJ-3GEYJ271V | DIGIKEY | P270GCT-ND | N/A
27 | 1 | R76 | RES 113 OHM 1/10W 1% 0603 SMD | PANASONIC - ECG | ERJ-3EKF1130V | DIGIKEY | P113HCT-ND | N/A
28 | 1 | R77 | RES 2.05K OHM 1/10W 1% 0603 SMD | ERJ-3EKF2051V | Panasonic | DIGIKEY | P2.05KHCT-ND | N/A
29 | 1 | R78 | RES 8.06K OHM 1/10W 1% 0603 SMD | ERJ-3EKF8061V | Panasonic | DIGIKEY | P8.06KHCT-ND | N/A
30 | 2 | TP1, TP2 | TEST POINT PC MINI .040"D RED | KEYSTONE ELECTRONICS | 5000 | DIGIKEY | 5000K-ND | N/A
31 | 1 | TP3 | TEST POINT PC MINI .040"D BLACK | KEYSTONE ELECTRONICS | 5001 | DIGIKEY | 5001K-ND | N/A
32 | 4 | U1, U3, U8, U9 | IC DRIVER MICROSTEPPING 28-TSSOP | ALLEGRO | A3979SLPTR-T | DIGIKEY | 620-1148-1-ND | N/A
33 | 1 | U2 | IC, OPTOCOUPLER, QUAD, 1-DIRECTION | AVAGO TECHNOLOGIES | ACSL-6400-00TE | DIGIKEY | 516-1603-5-ND | N/A
34 | 2 | U4, U10 | IC, OPTOCOUPLER, TRIPLE, 1-DIRECTION | AVAGO TECHNOLOGIES | ACSL-6300-50TE | MOUSER ELECTRONICS | 630-ACSL-6300-50TE | N/A
35 | 2 | U5, U6 | IC DUAL 1OF4 MUX/DEMUX 16TSSOP | TEXAS INSTRUMENTS | SN74CBT3253PWR | DIGIKEY | 296-1167-1-ND | N/A
36 | 1 | U7 | IC REGULATOR POS 5V D2PAK | STMICROELECTRONICS | L7805CD2T-TR | DIGIKEY | 497-1171-1-ND | N/A
37 | 1 | U11 | IC OP AMP 3.4MA 215MHZ SOT23-6 | Linear | LT6230CS6#TRMPBF | DIGIKEY | LT6230CS6#TRMPBFCT-ND | N/A
38 | 1 | HS1 | BOARD LEVEL HEATSINK .45" D-PAK | AAVID THERMALLOY | 7109DG | DIGIKEY | HS406-ND | N/A
 |  |  |  |  |  |  |  |  |  |  | bbm

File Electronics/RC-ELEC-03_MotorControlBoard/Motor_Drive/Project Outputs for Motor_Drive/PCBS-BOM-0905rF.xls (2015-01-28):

 | BILL OF MATERIALS FOR ELECTRONICS |  |  |  |  |  |  |  |  |  | Form #: IT 403G
 | Idaho Technology Inc. |  |  |  |  |  |  |  |  |  | Rev.: 01
 |  |  |  |  |  |  |  |  |  |  | Date Effective: 3/18/05
Approvals
Development Manager |  |  | Date | Production Manager |  |  | Date | QA |  |  | Date
Part #: | PCBS-BOM-0905 |  | Title: | Motor Drive BOM |  |  |  |  | Revision: | F
Project: | Plate Cycler |  | Master Assembly Number: |  | PCBA-SUB-0905 |  |  |  | Effective Date: | 2009-08-30
Quantity | Designator | #Column Name Error:Comment | Description |  | Manufacturer | Manufacturer P/N | Vendor | Vendor P/N | #Column Name Error:Notes
4 | C1, C2, C33, C34 |  | CAPACITOR TANT 100UF 25V 20% SMD |  | Kemet | T510E107M025AT E050 | Digikey | 399-3989-1-ND
8 | C3, C4, C5, C6, C35, C36, C37, C38 |  | CAP 56UF 50V ELECT FC RADIAL |  | Panasonic | EEU-FC1H560 | Digikey | P10322-ND
25 | C7, C8, C9, C10, C11, C12, C19, C20, C25, C27, C31, C39, C40, C41, C42, C43, C44, C52, C53, C58, C59, C60, C61, C62, C63 |  | CAP CER .10UF 50V X7R 0603 |  | Taiyo Yuden | UMK107B7104KA-T | Digikey | 587-1243-1-ND
12 | C13, C14, C15, C16, C17, C18, C46, C47, C48, C49, C50, C51 |  | CAP CER .22UF 50V Y5V 0603 |  | Murata Electronics North America | GRM188F51H224ZA01D | Digikey | 490-1569-1-ND
8 | C21, C22, C23, C24, C54, C55, C56, C57 |  | CAP 1000PF 50V CERAMIC X7R 0603 |  | Panasonic - ECG | ECJ-1VB1H102K | Digikey | PCC1772CT-ND
6 | C26, C28, C64, C65, C66, C67 |  | CAP CER 1.0UF 10V X5R 10% 0603 |  | TDK Corporation | C1608X5R1A105K | DIGIKEY | 445-1321-1-ND
1 | C29 |  | CAP .1UF 50V CERM CHIP 1206 X7R |  | PANASONIC | ECJ-3VB1H104K | DIGIKEY | PCC104BCT-ND
1 | C30 |  | CAP TANTALUM 10UF 50V 20% SMD |  | KEMET | B45196H7106M509 | DIGIKEY | 495-2288-1-ND
1 | C32 |  | CAP CER .33UF 50V X7R 0805 |  | MURATA ELECTRONICS | GRM219R71H334KA88D | Digikey | 490-3327-1-ND
1 | C45 |  | CAP 560UF 50V ELECT FC RADIAL |  | Panasonic | EEU-FC1H561 | Digikey | P11261-ND
1 | C68 |  | CAP 10000PF 50V CERM X7R 0603 |  | Panasonic | ECJ-1VB1H103K | Digikey | PCC1784CT-ND
1 | C69 |  | CAP 1.0UF 50V CERAMIC X7R 1210 |  | Kemet | C1210C105K5RACTU | DIGIKEY | 399-3076-1-ND
1 | C70 |  | CAP CER 22UF 16V X7R 20% 1812 |  | TDK | C1210C105K5RACTU | DIGIKEY | 445-1442-1-ND
2 | D1, D3 |  | DIODE SUPER FAST REC 2A 100V SMB |  | Diodes Inc. | ES2B-13-F | Digikey | ES2B-FDICT-ND
1 | D2 |  | LED 565NM GRN DIFF 0603 SMD |  | Lumex Opto/Components Inc | SML-LX0603GW-TR | Digikey | 67-1549-1-ND
1 | F1 |  | FUSEBLOCK W/.375A FUSE SMD FST |  | Littelfuse Inc | 0154.375DR | Digikey | F3150CT-ND
1 | F2 |  | FUSEBLOCK W/2A FUSE SMD FAST |  | Littelfuse Inc | 0154002.DR | Digikey | F1224CT-ND
4 | J1, J2, J4, J5 |  | CONN HEADER 4POS .100 VERT GOLD |  | Molex/Waldom Electronics Corp | 70543-0003 | Digikey | WM4802-ND
1 | J3 |  | CONN HEADER 3POS .100 VERT GOLD |  | MOLEX | 70543-0002 | DIGIKEY | WM4801-ND
6 | J6, J7, J8, J9, J10, J11 |  | CONN HEADER 5POS .100 VERT GOLD |  | Molex | 70543-0004 | Digikey | WM4803-ND
1 | L1 |  | POWER INDUCTOR 100UH 1.3A SMD |  | Sumida Corporation | CDRH125NP-101MC | Digikey | 308-1437-1-ND
1 | P1 |  | CONN HEADER 12POS 2MM PCB TIN |  | HIROSE | DF11-12DP-2DSA(24) | DIGIKEY | H10233-ND
8 | R1, R4, R5, R12, R37, R40, R48, R50 |  | RES 0.0 OHM 1/10W 5% 0603 SMD |  | ROHM SEMICONDUCTOR | MCR03EZPJ000 | DIGIKEY | RHM0.0GCT-ND
24 | R3, R6, R7, R9, R24, R25, R27, R28, R33, R34, R35, R39, R42, R43, R45, R72, R74, R79, R80, R81, R82, R83, R84, R91 |  | RES 1.00K OHM 1/10W 1% 0603 SMD |  | PANASONIC, PANASONIC - ECG | ERJ-3EKF1001V | DIGIKEY | P1.00KHCT-ND
7 | R8, R10, R44, R46, R69, R70, R71 |  | RES 10K OHM 1/10W 5% 0603 SMD |  | Panasonic | ERJ-3GEYJ103V | Digikey | P10KGCT-ND
8 | R15, R16, R17, R18, R51, R52, R53, R54 |  | RES 12.7K OHM 1/10W 1% 0603 SMD |  | Panasonic | ERJ-3EKF1272V | Digikey | P12.7KHCT-ND
8 | R19, R20, R21, R22, R55, R56, R57, R58 |  | RES .56 OHM 1W 1% 2512 SMD |  | Panasonic | ERJ-1TRQFR56U | Digikey | PT.56YCT-ND
9 | R23, R26, R29, R30, R31, R32, R36, R73, R75 |  | RES 237 OHM 1/10W 1% 0603 SMD |  | PANASONIC - ECG | ERJ-3EKF2370V | DIGIKEY | P237HCT-ND
7 | R59, R60, R61, R62, R63, R64, R76 |  | RES 270 OHM 1/10W 5% 0603 SMD |  | Panasonic | ERJ-3GEYJ271V | Digikey | P270GCT-ND
4 | R77, R85, R86, R89 |  | RES 10.0K OHM 1/10W 1% 0603 SMD |  | Panasonic | ERJ-3EKF1002V | Digikey | P10.0KHCT-ND
4 | R78, R87, R88, R90 |  | RES 8.06K OHM 1/10W 1% 0603 SMD |  | Panasonic | ERJ-3EKF8061V | Digikey | P8.06KHCT-ND
1 | R92 |  | RES 5.62K OHM 1/10W 1% 0603 SMD |  | Panasonic | ERJ-3EKF5621V | Digikey | P5.62KHCT-ND
3 | TP1, TP2, TP4 |  | TEST POINT PC MINI .040"D RE |  | KEYSTONE ELECTRONICS | 5000 | DIGIEKY, Digikey | 5000K-ND
1 | TP3 |  | TEST POINT PC MINI .040"D BLACK |  | KEYSTONE ELECTRONICS | 5001 | DIGIKEY | 5001K-ND
4 | U1, U3, U8, U9 |  | IC DRIVER MICROSTEPPING 28-TSSOP |  | ALLEGRO | A3979SLPTR-T | DIGIKEY | 620-1148-1-ND
1 | U2 |  | OPTOCOUPLER QUAD 15MBD 16-SOIC |  | AVAGO TECHNOLOGIES | ACSL-6400-00TE | DIGIKEY | 516-1603-5-ND
2 | U4, U10 |  | Optocouplers 3.0V - 5.5V 15MBd |  | AVAGO TECHNOLOGIES | ACSL-6300-50TE | MOUSER ELECTRONICS | 630-ACSL-6300-50TE
2 | U5, U6 |  | IC DUAL 1OF4 MUX/DEMUX 16TSSOP |  | TEXAS INSTRUMENTS | SN74CBT3253PWR | DIGIKEY | 296-1167-1-ND
1 | U7 |  | IC REGULATOR POS 5V D2PAK |  | STMicroelectronics | L7805CD2T-TR | DIGIKEY | 497-1171-1-ND
1 | U11 |  | IC REG SIMPLE SWITCHER 8-SOIC |  | National Semiconductor | LM2675M-ADJ/NOPB | Digikey | LM2675M-ADJ-ND

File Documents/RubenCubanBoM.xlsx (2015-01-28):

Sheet: BoM
Ruben Cuban Part # | Part Description | Quantity | Vendor | Vendor Part Number | Price/Unit | Total Cost
RC-MECH-01 | Socket | 6 | 3D Print @ BioFire | N/A | $0.00 | $0.00
RC-MECH-02 | Sensor Mount | 6 | 3D Print @ BioFire | N/A | $0.00 | $0.00
RC-MECH-03 | Shaft | 6 | 3D Print @ BioFire | N/A | $0.00 | $0.00
RC-MECH-04 | Stepper Motor | 6 | BioFire Scrap | N/A | $0.00 | $0.00
RC-MECH-05 | Air Cylinder | 6 | Amico | a12030500ux0057 | $7.86 | $47.16
RC-MECH-06 | Solenoid Valve | 6 | uxcell | a11102700ux0130 | $10.31 | $61.86
RC-MECH-07 | Pin | 6 | McMaster-Carr | 91259A109 | $4.76 | $28.56
RC-MECH-08 | Pin Bumper | 6 | BioFire Scrap | N/A | $0.00 | $0.00
RC-MECH-09 | Spring | 6 | McMaster-Carr | 94125K839 | $2.66 | $15.96
RC-MECH-10 | Slide | 6 | BioFire Scrap | N/A | $0.00 | $0.00
RC-MECH-11 | Back Plate | 6 | BioFire Scrap | N/A | $0.00 | $0.00
RC-MECH-12 | Terminal Block | 1 | DigiKey | 283-4016-ND | $4.29 | $4.29
RC-MECH-13 | Terminal Block Jumper | 1 | DigiKey | WM9718-ND | $2.86 | $2.86
RC-MECH-14 | Hard Drive Mount | 1 | BioFire Scrap | N/A | $0.00 | $0.00
RC-MECH-15 | 4mm Tubing 10M | 1 | uxcell | a12022000ux0121 | $7.13 | $7.13
RC-MECH-16 | Air Cylinder Push In Connector | 12 | uxcell | N/A | $2.04 | $24.48
RC-MECH-17 | Air Compressor | 1 | Harbor Freight | 97080 | $54.99 | $54.99
RC-MECH-18 | 1/4" to 4mm(5/32) Fitting | 26 | Fastenal | 443066 | $1.64 | $42.64
RC-MECH-19 | Snap Action Switch | 12 | BioFire Scrap | N/A | $0.00 | $0.00
RC-ELEC-01 | Power Supply | 1 | BioFire Scrap | N/A | $0.00 | $0.00
RC-ELEC-02 | System Control Board | 1 | BioFire Scrap | N/A | $0.00 | $0.00
RC-ELEC-03 | Motor Control Board | 2 | BioFire Scrap | N/A | $0.00 | $0.00
RC-ELEC-04 | Single Board Computer | 1 | BioFire Scrap | N/A | $0.00 | $0.00
RC-ELEC-05 | Hard Drive | 1 | BioFire Scrap | N/A | $0.00 | $0.00
RC-ELEC-06 | Relay Board | 1 | SainSmart | 20-018-102 | $11.99 | $11.99
RC-ELEC-07 | LCD Screen | 1 | BioFire Scrap | N/A | $0.00 | $0.00
RC-ELEC-08 | Mini Atx Power Supply | 1 | BioFire Scrap | N/A | $0.00 | $0.00
RC-ELEC-09 | Break Sensor | 6 | BioFire Scrap | N/A | $0.00 | $0.00
RC-WIRE-01 | Hard Drive Power Cable | 1 | BioFire Scrap | N/A | $0.00 | $0.00
 |  |  |  |  | Total Cost | $301.92

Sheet: Purchase History
Item | Date | Part Number | Cost | Supplier | Qty | Dylan | Matt
Amico 4V210-08 DC 24V 2 Position 5 Way Pneumatic Solenoid Valve | 2014-05-21 | s13101200am0196 | $15.50 | uxcell | 1 | $15.50
2 of 1/4" PT Male Thread to 4mm Tube Push in Connect Straight Quick Fitting & 2 of 5/32" 4mm M4 Male Thread to Push In Connector Straight Pneumatic Quick Fitting | 2014-05-05 |  | $12.16 | uxcell | 2/2 | $12.16
Amico Black 4mm x 2.5mm Pneumatic Polyurethane PU Air Hose Tube 10M | 2014-05-05 |  | $12.31 | uxcell | 1 | $12.31
1/4" Electric Solenoid Valve 12-Volt DC | 2014-05-05 | TK0398 | $8.50 | Sunweb | 1 | $8.50
5/32X1/4 M UNIConn Fitting for 1/4" NPT to 4mm(5/32) |  | 443066 | $15.46 | Fastenal | 5 |  | $15.46
Screw for prototype Pin | 2014-03-28 |  | $4.63 | Lowes | 1 | $4.63
Metric Compression Spring, Music Wire, 39MM Overall, 11.0MM OD, 1.00MM Wire | 2014-04-09 | 94125K839 | $18.89 | McMaster-Carr | 5 | $18.89
Pneumatic 12mmx25mm Double Action Thin Air Cylinder SDA 12-25 |  |  | $7.79 | uxcell | 1 |  | $7.79
Early Prototype Material | 2014-03-01 |  | $10.00 | Lowes | 1 |  | $10.00
3 gal. 1/3 HP 100 PSI Oilless Hotdog Air Compressor | 2014-06-14 | 97080 | $53.41 | Harbor Freight | 1 |  | $53.41
SainSmart 8-Channel Relay Module | 2014-06-17 |  | $20.00 | SainSmart | 1 | $20.00
Plexiglass Sheet | 2014-06-26 |  | $23.41 | Lowes | 1 | $23.41
Alloy Steel Shoulder Screw, 5/16" Dia X 2-1/2" Lg Shoulder, 1/4"-20 Thread / Plain Grade 2 Steel Hex Nut, 1/4"-20 Thread Size, 7/16" Width, 7/32" Height / Metric Compression Spring, Music Wire, 39mm Overall, 11.0mm Od, 1.00mm Wire | 2014-06-27 | 91259A109 / 90490A029 / 94125K839 | $51.69 | McMaster-Carr | 6 / 100 / 5 | $51.69
#2 * 5 and #9 * 5 | 2014-12-15 |  | $91.05 | uxcell | 5 of each |  | $91.05
8 slot terminal block with jumpers - TERM BLK 20A 4CIRC UL CSA/JUMPER EDGEON SQ 4POS .375 CNTR | 2014-12-15 | 283-4016-ND/WM9718-ND | $10.00 | DigiKey | 1/2 | $10.47
Dylan Total | $177.56
Matt Total | $177.71
Total | $354.80

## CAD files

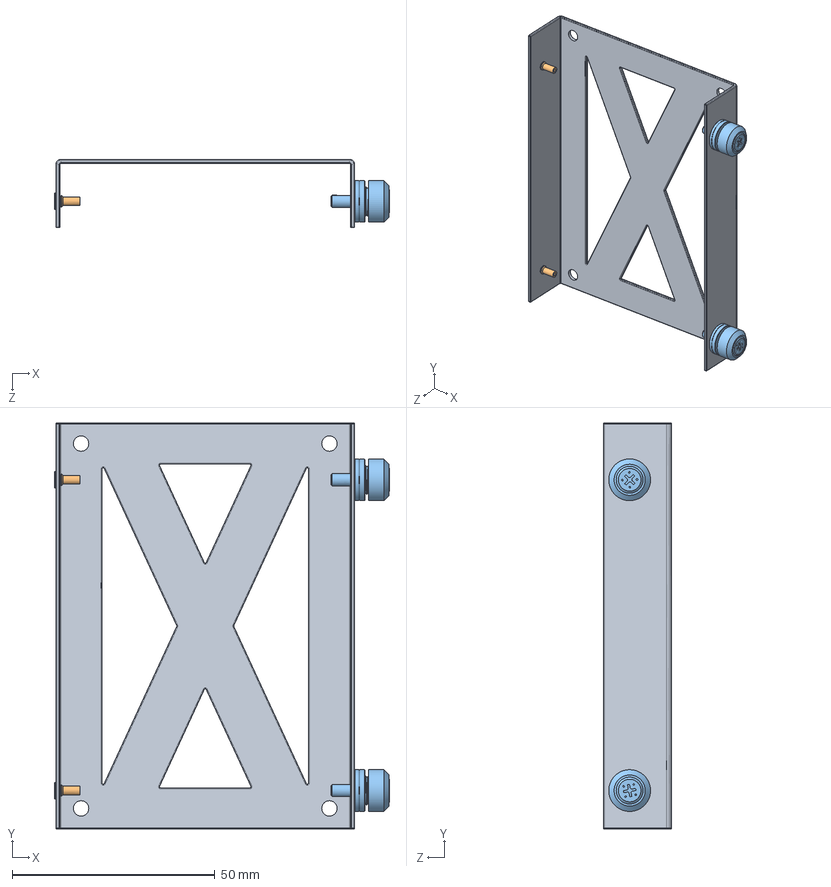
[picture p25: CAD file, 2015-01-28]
Mechanical/RC-MECH-14_HardDriveMount/PCYC-SMT-0055_Hard_Drive_Mount_Bracket/PCYC-SMT-0055_03_PCYC-SMT-0055.SLDASM
82.7 x 100.1 x 16.9 mm
PCYC-SMT-0055
FHA-084-4 x 2
PF50-M3-0 CN x 2

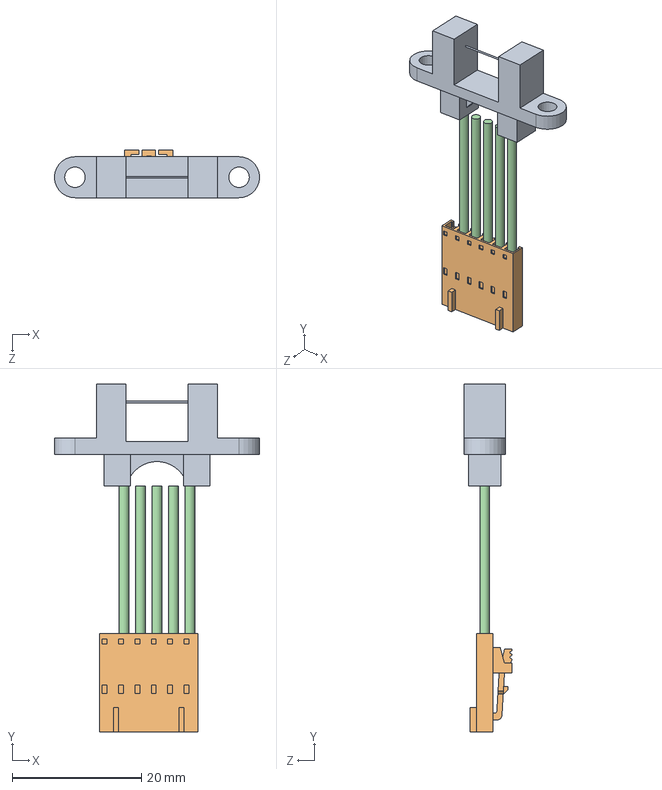
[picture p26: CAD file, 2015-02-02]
Mechanical/HerbertAssembly/22WIRE-HAR-0619.SLDASM
31.8 x 53.8 x 7.35 mm
22OPB911W55Z
22WIRE-HAR-0619

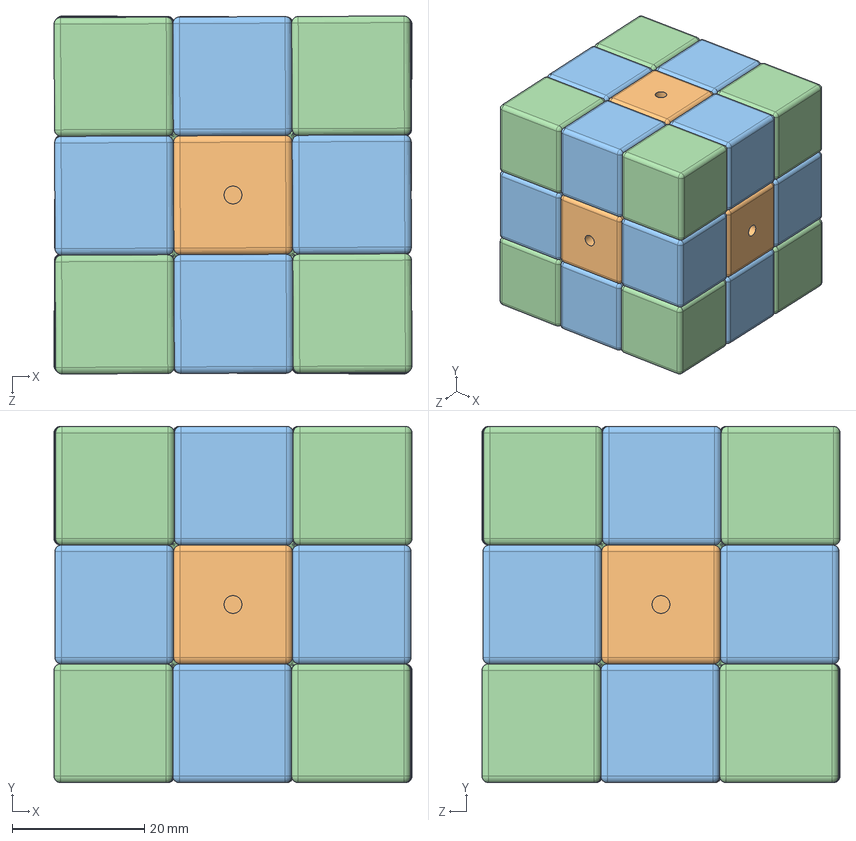
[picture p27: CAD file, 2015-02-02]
Mechanical/HerbertAssembly/22Assem1.SLDASM
54.2 x 54.0 x 54.2 mm
22Center Block
22Center x 6
22Edge x 12
22Corner x 8

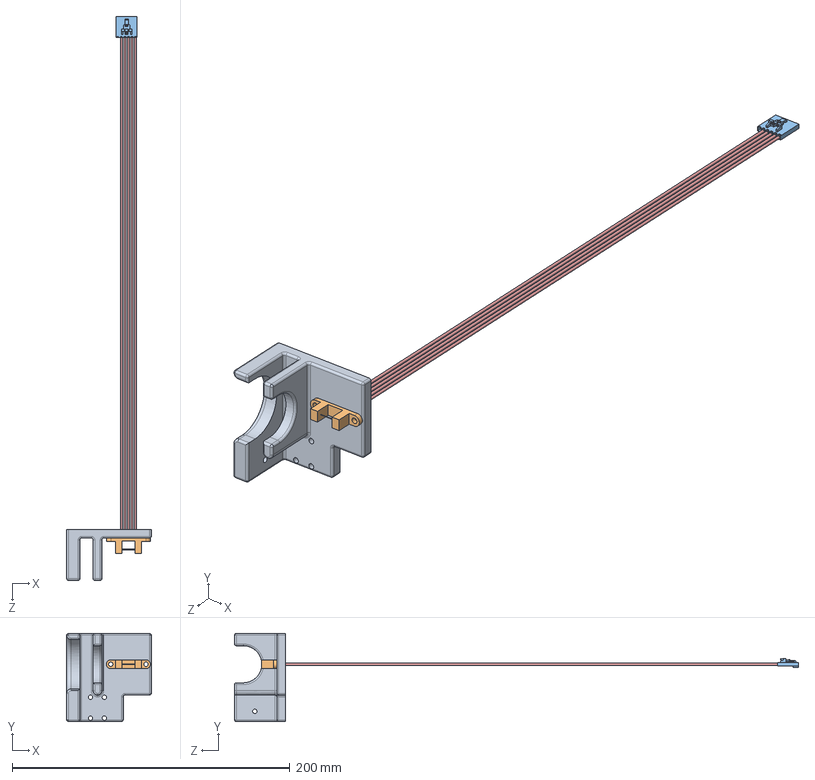
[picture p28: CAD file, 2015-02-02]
Mechanical/HerbertAssembly/pusher aasembly.SLDASM
61.0 x 63.5 x 406.1 mm
pusher
22OPB911W55Z
22WIRE-HAR-0619

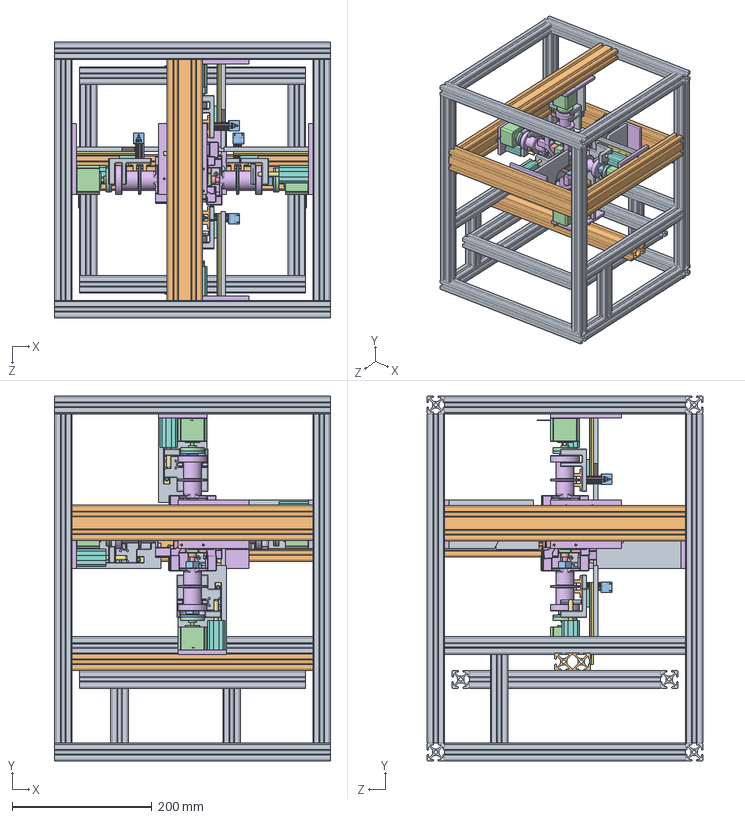
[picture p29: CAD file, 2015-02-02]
Mechanical/HerbertAssembly/final frame.SLDASM
394.7 x 521.7 x 394.7 mm
10-10 frame x 23
10-20 frame x 6
shaft x 6
22MOTR-DCM-2013 x 6
spring pin x 6
arm x 6
22Shaft x 6
22Air Cylinder x 6
pusher x 6
22OPB911W55Z x 6
22WIRE-HAR-0619 x 6
back plate x 6
22HI_RSR9KM1957.52 Track x 6
slide mount x 6
bearing plateform x 6
22Center Block
22Center x 6
22Edge x 12
22Corner x 8

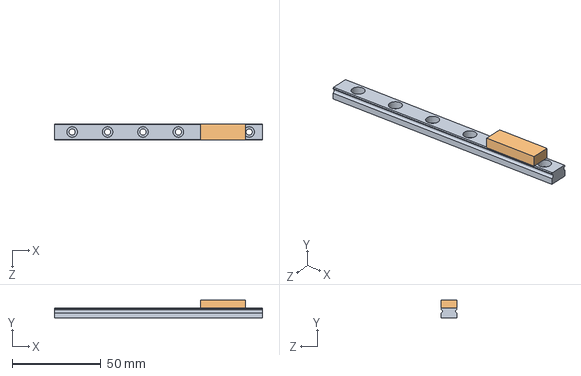
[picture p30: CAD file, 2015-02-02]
Mechanical/HerbertAssembly/22Slide mount.SLDASM
117.5 x 10.1 x 9.00 mm
22HI_RSR9KM1957.52 Track
slide mount

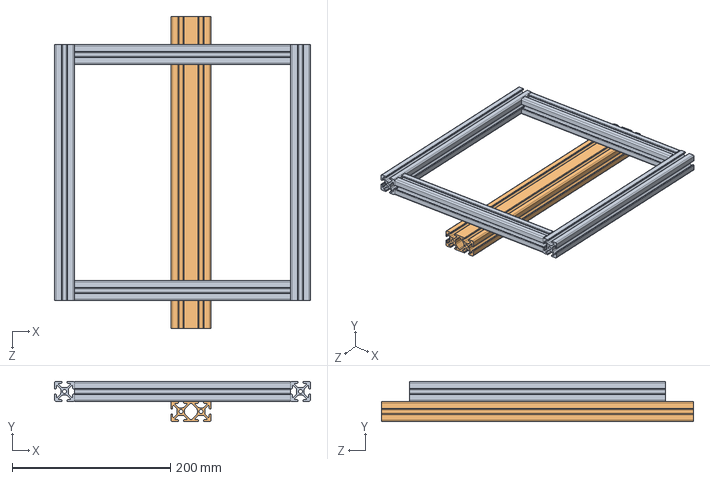
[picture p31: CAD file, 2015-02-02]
Mechanical/HerbertAssembly/slide door.SLDASM
323.6 x 50.8 x 394.7 mm
10-10 frame x 4
10-20 frame

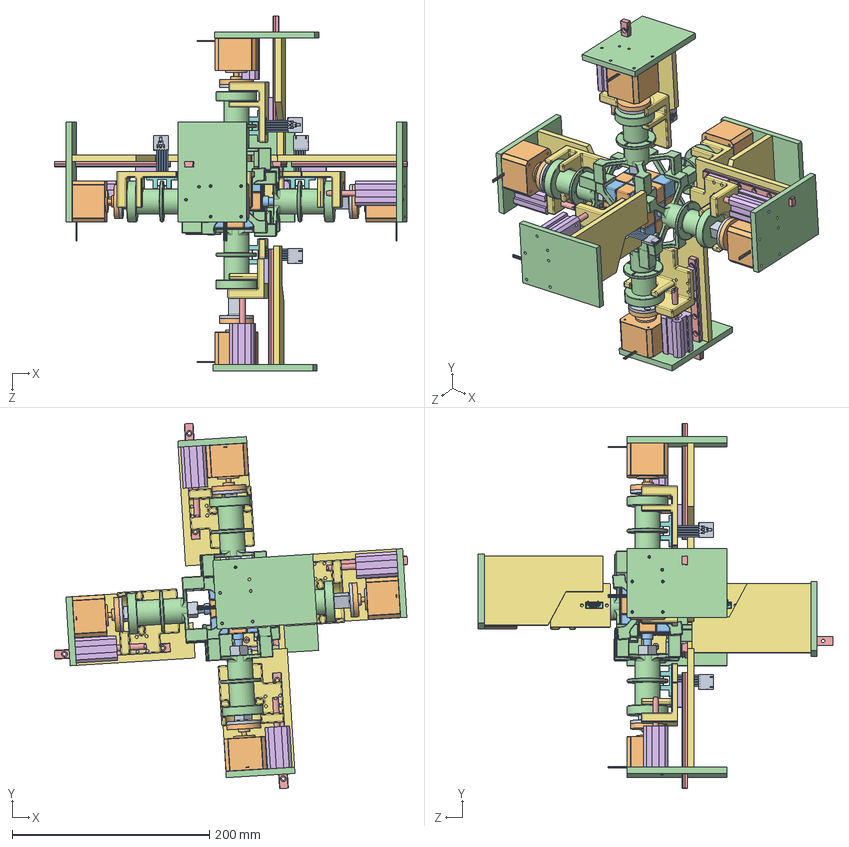
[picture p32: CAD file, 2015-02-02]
Mechanical/HerbertAssembly/Assem2.SLDASM
358.3 x 370.5 x 360.0 mm
shaft x 6
22MOTR-DCM-2013 x 6
spring pin x 6
arm x 6
22Shaft x 6
22Air Cylinder x 6
pusher x 6
22OPB911W55Z x 6
22WIRE-HAR-0619 x 6
back plate x 6
22HI_RSR9KM1957.52 Track x 6
slide mount x 6
bearing plateform x 6
22Center Block
22Center x 6
22Edge x 12
22Corner x 8

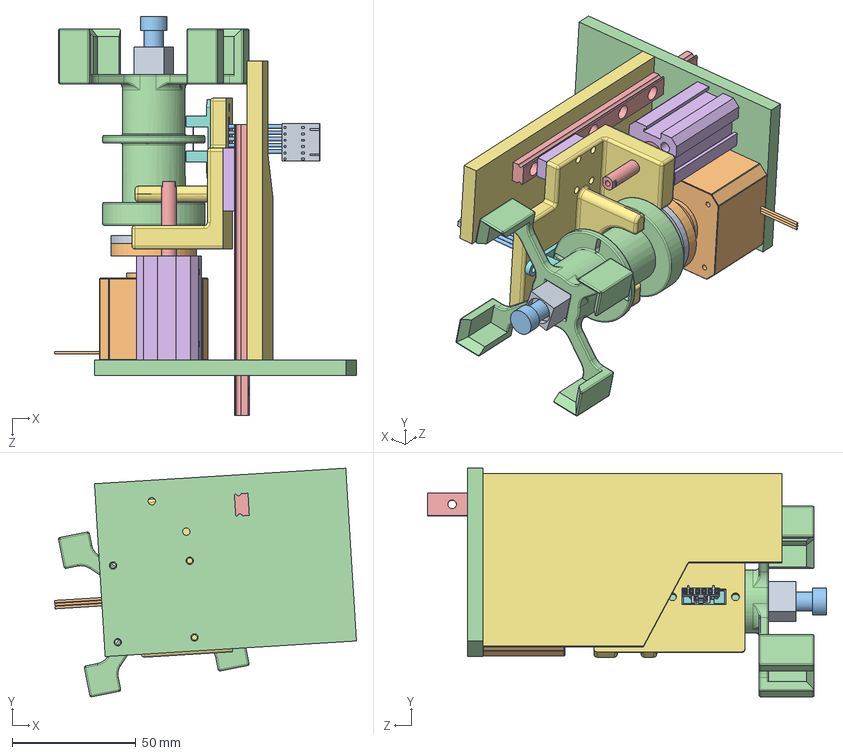
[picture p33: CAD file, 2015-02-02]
Mechanical/HerbertAssembly/Assem1.SLDASM
121.8 x 92.2 x 161.0 mm
shaft
22MOTR-DCM-2013
spring pin
arm
22Shaft
22Air Cylinder
pusher
22OPB911W55Z
22WIRE-HAR-0619
back plate
22HI_RSR9KM1957.52 Track
slide mount
bearing plateform

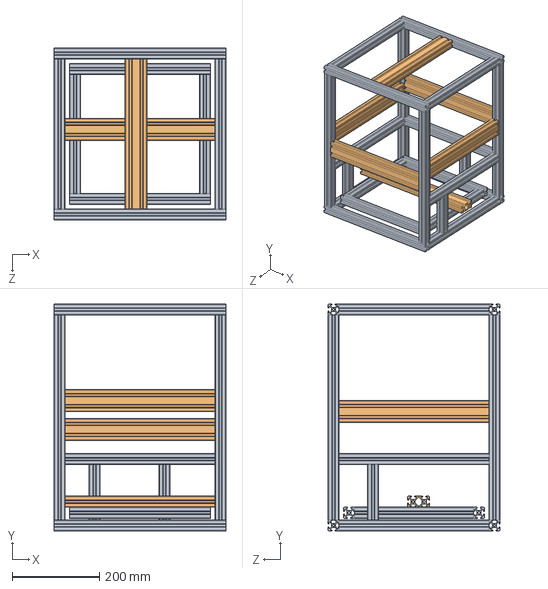
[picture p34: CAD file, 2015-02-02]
Mechanical/HerbertAssembly/frame assembly.SLDASM
394.7 x 521.7 x 394.7 mm
10-10 frame x 23
10-20 frame x 6

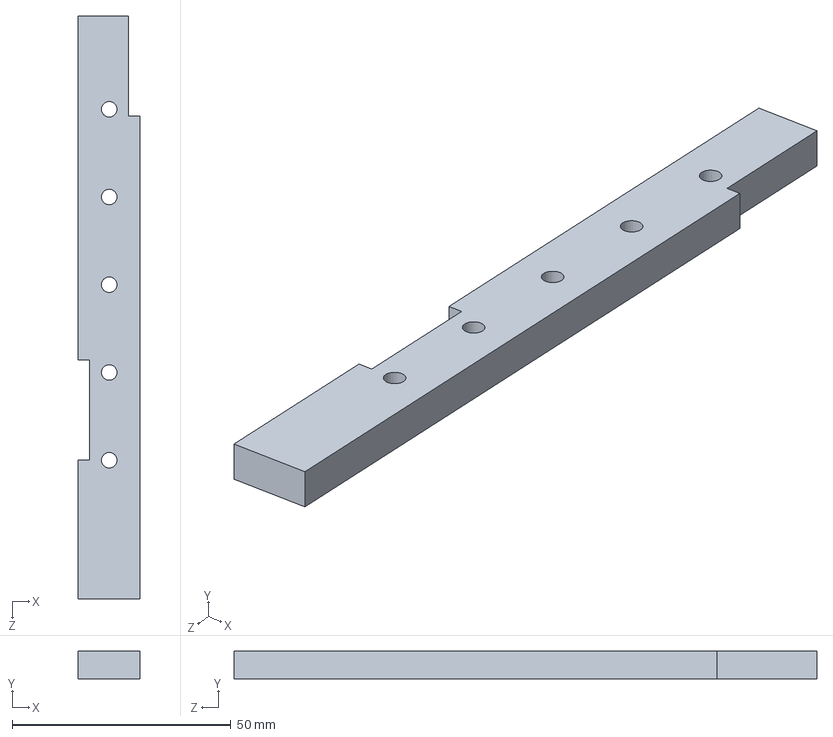
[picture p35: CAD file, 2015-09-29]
Mechanical/HerbertAssembly/bearing plateform2.SLDPRT
14.1 x 6.35 x 133.4 mm

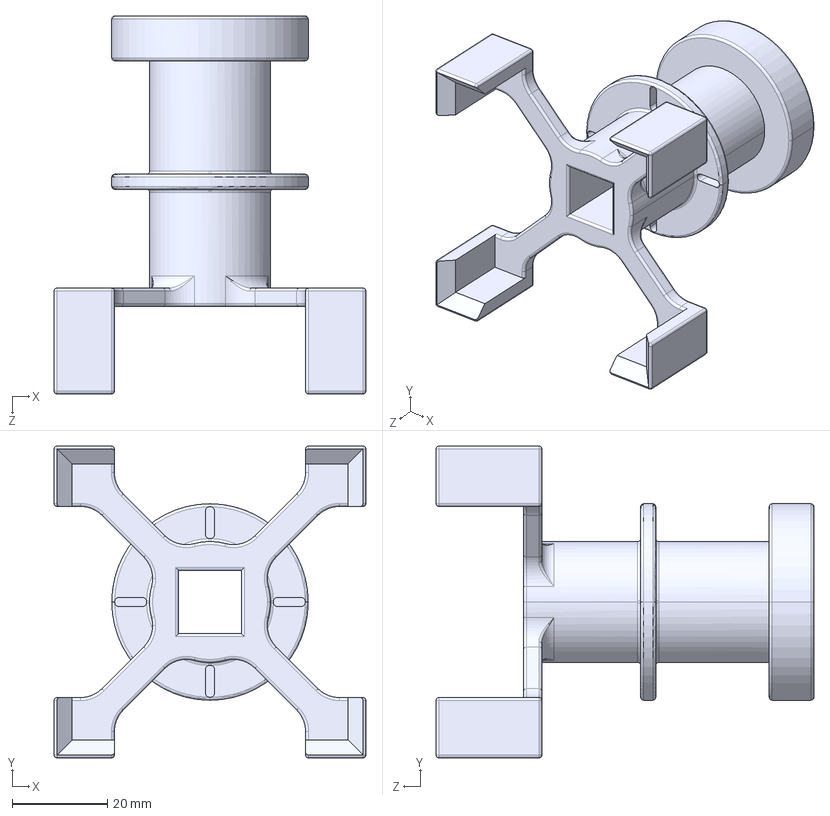
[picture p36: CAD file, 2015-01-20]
Mechanical/RC-MECH-01_Socket/arm.STEP
65.5 x 65.5 x 79.4 mm

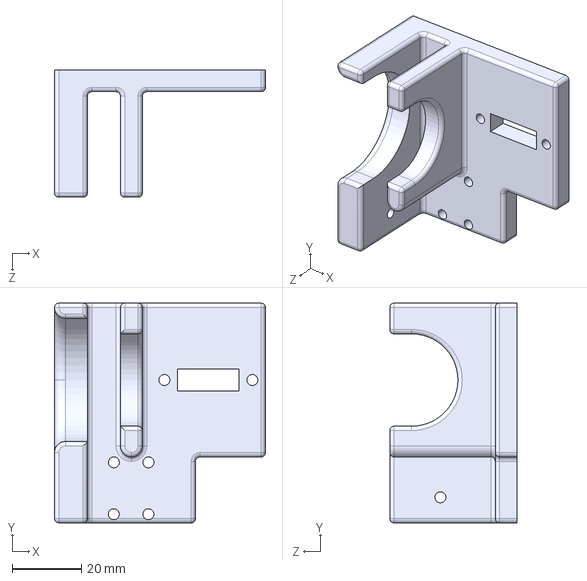
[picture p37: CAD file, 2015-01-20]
Mechanical/RC-MECH-02_SensorMount/SensorMount.STEP
61.0 x 63.5 x 36.8 mm

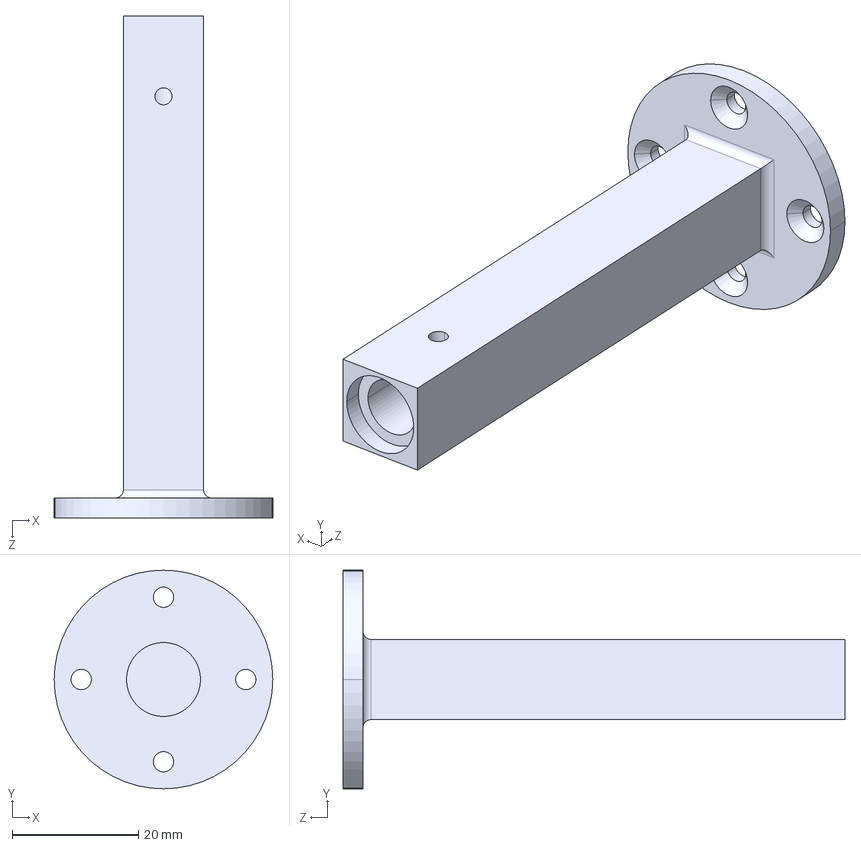
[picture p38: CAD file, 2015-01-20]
Mechanical/RC-MECH-03_Shaft/Shaft.STEP
34.6 x 34.6 x 79.4 mm

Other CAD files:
Mechanical/HerbertAssembly/22Air Cylinder OUT.SLDASM
Mechanical/RC-MECH-05_AirCylinder/1.sldprt
Mechanical/RC-MECH-10_Slide/rsr9zm.dxf
Mechanical/RC-MECH-10_Slide/RSR9ZMUU+195LM/RSR9KM21957_50030_800_2_03.stp
Mechanical/HerbertAssembly/10-10 frame.SLDPRT
Mechanical/HerbertAssembly/10-20 frame.SLDPRT
Mechanical/HerbertAssembly/22050579406.SLDPRT
Mechanical/HerbertAssembly/2216-02-0096.SLDPRT
Mechanical/HerbertAssembly/22Air Cylinder.SLDPRT
Mechanical/HerbertAssembly/22Center Block.SLDPRT
Mechanical/HerbertAssembly/22Center.SLDPRT
Mechanical/HerbertAssembly/22Corner.SLDPRT
Mechanical/HerbertAssembly/22Edge.SLDPRT
Mechanical/HerbertAssembly/22HI_RSR9KM1957.52 Track.sldprt
Mechanical/HerbertAssembly/22MOTR-DCM-2013.SLDPRT
Mechanical/HerbertAssembly/22OPB911W55Z.SLDPRT
Mechanical/HerbertAssembly/22Shaft.SLDPRT
Mechanical/HerbertAssembly/22WIRE-HAR-0619.SLDPRT
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

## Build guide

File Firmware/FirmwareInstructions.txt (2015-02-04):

Instructions for building and loading the firmware:

	1. Using GNU make, send "make app" command from the location $GitHubLocation\herbert\Firmware\firmware

	2. Next, send "make all" in $GitHubLocation\herbert\Firmware\

	3. A herbert_scb.bin should have been created in the same directory

	4. In Herbert Controller use the Upgrade Sys Ctrl Firmware... button and select the .bin file.

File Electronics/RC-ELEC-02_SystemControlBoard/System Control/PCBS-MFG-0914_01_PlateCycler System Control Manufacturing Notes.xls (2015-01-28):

 | Manufacturing Notes for Electronics |  |  |  |  |  |  | Form #: IT 403H
 | Idaho Technology Inc. |  |  |  |  |  |  | Rev.: 03
 |  |  |  |  |  |  |  | Date Effective: 3/18/05
Approvals
Development Manager |  | Date | Production Manager |  | Date | QA |  | Date
Part #: | PCBS-MFG-0914 | Title: | PlateCycler System Control Manufacturing Notes |  |  |  | Revision: | 01
Project: | PlateCycler | Master Assembly Number: |  | PCBA-SUB-0914 |  |  | Effective Date:
Step | Description | Specification |  |  |  |  | Notes
1 | Board Material | Per IPC-4101A/24/26/29/99, copper clad, high temperature FR4 class epoxy glass rated UL94V-0 |  |  |  |  | Must be RoHS compliant and survive a lead-free assembly max reflow of 260 degrees C (6 passes) - Td rating > 340 degrees C - Z axis CTE < 3.5% - Tg > 170 Degrees C
2 | Layer Order | Top, GND 2, Signal 3, Signal 4, 3.3V 5, Signal 6 Signal 7, 2.5V 8, Signal 9, Signal 10, GND 11, Bottom |  |  |  |  | -
3 | Tolerance | IPC-A-6011 and IPC-6012 Class 2 |  |  |  |  | -
4 | Board Thickness | 0.062" |  |  |  |  | Finished board thickness
5 | Hole Sizes | Hole Sizes are After Plating |  |  |  |  | -
6 | Solder Mask | SMOBC per IPC-SM-840C, class T |  |  |  |  | Must be RoHS compliant, type LIP, green or equivalent
7 | Copper Weight | 1/2 ounce |  |  |  |  | -
8 | Copper Thieving | Vendor may add copper thieving as needed to improve manufacturability |  |  |  |  | -
9 | Board Warp | Maximum allowable board warp or twist is 0.005 per inch, determined using any of the measurement techniques in IPC-A-600-B |  |  |  |  | -
10 | Finish | Plated with Immersion Gold over Electroless Nickel over copper (NiAu), 3 - 7 micro inches gold over minimum 100 micro inches nickel. |  |  |  |  | -
11 | Silkscreen | Nonconductive, white, RoHS compliant ink |  |  |  |  | Apply to both top and bottom; not allowed on component pads or mounting holes
12 | Electrical Test | Test each PCB 100% for opens and shorts |  |  |  |  | -
13 | PCBA Number | Sticker or Permanent Ink |  |  |  |  | The Master Assembly Number (PCBA-SUB-0914) is printed in silkscreen on the PCB along with a silkscreen block. In that block, either write the Assembly revision number (01) OR affix a sticker with the Assembly revision number. Place the rev number to the completed, populated circuit board.
14 | Serial Number | Sticker |  |  |  |  | A serial number sticker should be applied to the completed, populated circuit board assembly.
15 | Inspection/Testing | Optical inspection |  |  |  |  | Optical inspection should be done on the completed, populated circuit board assembly. Either a stamp or a sticker should be applied to indicate the inspection has been done.
16 | Flame Rating | UL 94V-0 |  |  |  |  | The flame rating should be stamped on the bare circuit board.
17 | Controlled Trace-GND impedence | Control trace-to-GND impedance on all 4.106 mil wide traces to 50 ohms +/- 10% on all signal layers |  |  |  |  | -

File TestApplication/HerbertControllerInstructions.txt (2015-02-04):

Instructions for building Herbert Controller GUI:

	1. In Visual Studio 2012 open the HerbertController.sln

	2. In the Herbert Controller Project Properties, Configuration set to Active(Debug), Platform set to Active(Win32), 
           Under Configuration Properties, General, set the platform toolset to Visual Studio 2012 - Windows XP (v110_xp). 
           (You may need to download this toolset).
	
	3. Build in Debug, Win32

	4. The .exe will be generated in the $GithubLocation\herbert\TestApplication\HerbertController\Debug

	5. Place this .exe onto the single board computer to run it.

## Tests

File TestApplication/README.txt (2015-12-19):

This folder contains the code for our debug gui application that sends commands over to the fpga

boost 
	- contains the boost library (third party)

HerbertController
	- contains the visual studio project and all of the source code for this application (we modified an existing application for our needs)

HerberControllerInstructions.txt
	- instructions on how to build the gui app inside of visual studio

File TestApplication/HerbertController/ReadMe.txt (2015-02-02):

========================================================================
       MICROSOFT FOUNDATION CLASS LIBRARY : HerbertController
========================================================================

AppWizard has created this HerbertController application for you.  This application
not only demonstrates the basics of using the Microsoft Foundation classes
but is also a starting point for writing your application.

This file contains a summary of what you will find in each of the files that
make up your HerbertController application.

HerbertController.dsp
    This file (the project file) contains information at the project level and
    is used to build a single project or subproject. Other users can share the
    project (.dsp) file, but they should export the makefiles locally.

HerbertController.h
    This is the main header file for the application.  It includes other
    project specific headers (including Resource.h) and declares the
    CHerbertControllerApp application class.

HerbertController.cpp
    This is the main application source file that contains the application
    class CHerbertControllerApp.

HerbertController.rc
    This is a listing of all of the Microsoft Windows resources that the
    program uses.  It includes the icons, bitmaps, and cursors that are stored
    in the RES subdirectory.  This file can be directly edited in Microsoft
	Visual C++.

HerbertController.clw
    This file contains information used by ClassWizard to edit existing
    classes or add new classes.  ClassWizard also uses this file to store
    information needed to create and edit message maps and dialog data
    maps and to create prototype member functions.

res\HerbertController.ico
    This is an icon file, which is used as the application's icon.  This
    icon is included by the main resource file HerbertController.rc.

res\HerbertController.rc2
    This file contains resources that are not edited by Microsoft 
	Visual C++.  You should place all resources not editable by
	the resource editor in this file.

/////////////////////////////////////////////////////////////////////////////

AppWizard creates one dialog class:

HerbertControllerDlg.h, HerbertControllerDlg.cpp - the dialog
    These files contain your CHerbertControllerDlg class.  This class defines
    the behavior of your application's main dialog.  The dialog's
    template is in HerbertController.rc, which can be edited in Microsoft
	Visual C++.

/////////////////////////////////////////////////////////////////////////////
Other standard files:

StdAfx.h, StdAfx.cpp
    These files are used to build a precompiled header (PCH) file
    named HerbertController.pch and a precompiled types file named StdAfx.obj.

Resource.h
    This is the standard header file, which defines new resource IDs.
    Microsoft Visual C++ reads and updates this file.

/////////////////////////////////////////////////////////////////////////////
Other notes:

AppWizard uses "TODO:" to indicate parts of the source code you
should add to or customize.

If your application uses MFC in a shared DLL, and your application is 
in a language other than the operating system's current language, you
will need to copy the corresponding localized resources MFC42XXX.DLL
from the Microsoft Visual C++ CD-ROM onto the system or system32 directory,
and rename it to be MFCLOC.DLL.  ("XXX" stands for the language abbreviation.
For example, MFC42DEU.DLL contains resources translated to German.)  If you
don't do this, some of the UI elements of your application will remain in the
language of the operating system.

/////////////////////////////////////////////////////////////////////////////

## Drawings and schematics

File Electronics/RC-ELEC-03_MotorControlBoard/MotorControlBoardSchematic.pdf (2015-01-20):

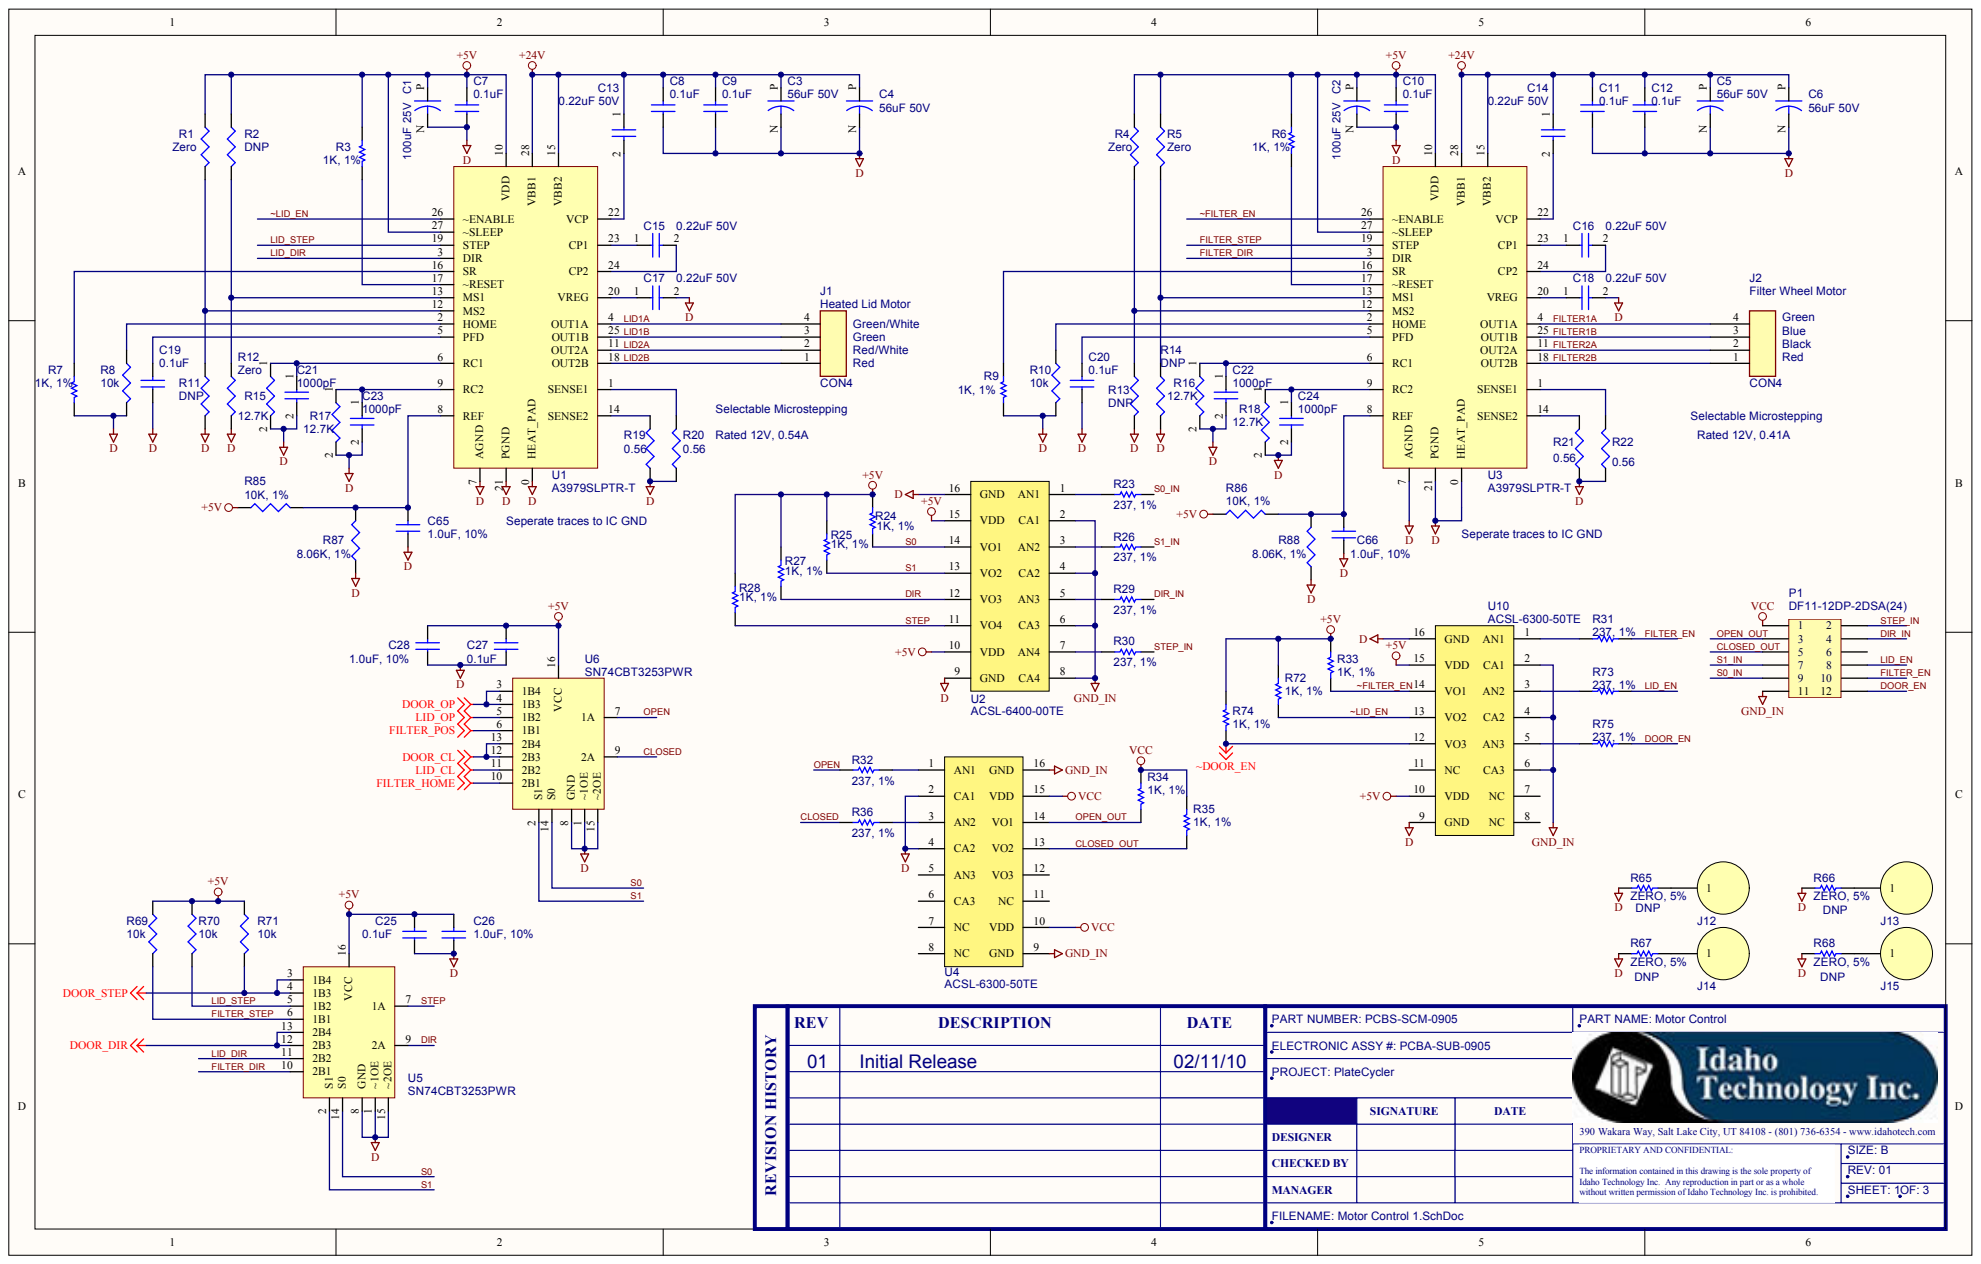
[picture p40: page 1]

Seperate traces to IC GND

LID_STEP | | 1B2 5

ELECTRONIC ASSY #: PCBA-SUB-0905

SIGNATURE | DATE

390 Wakara Way, Salt Lake City, UT 84108 - (801) 736-6354 - www.idahotech.com

DESIGNER

The information contained in this drawing is the sole property of
Idaho Technology Inc. Any reproduction in part or as a whole

FILENAME: Motor Control 1.SchDoc

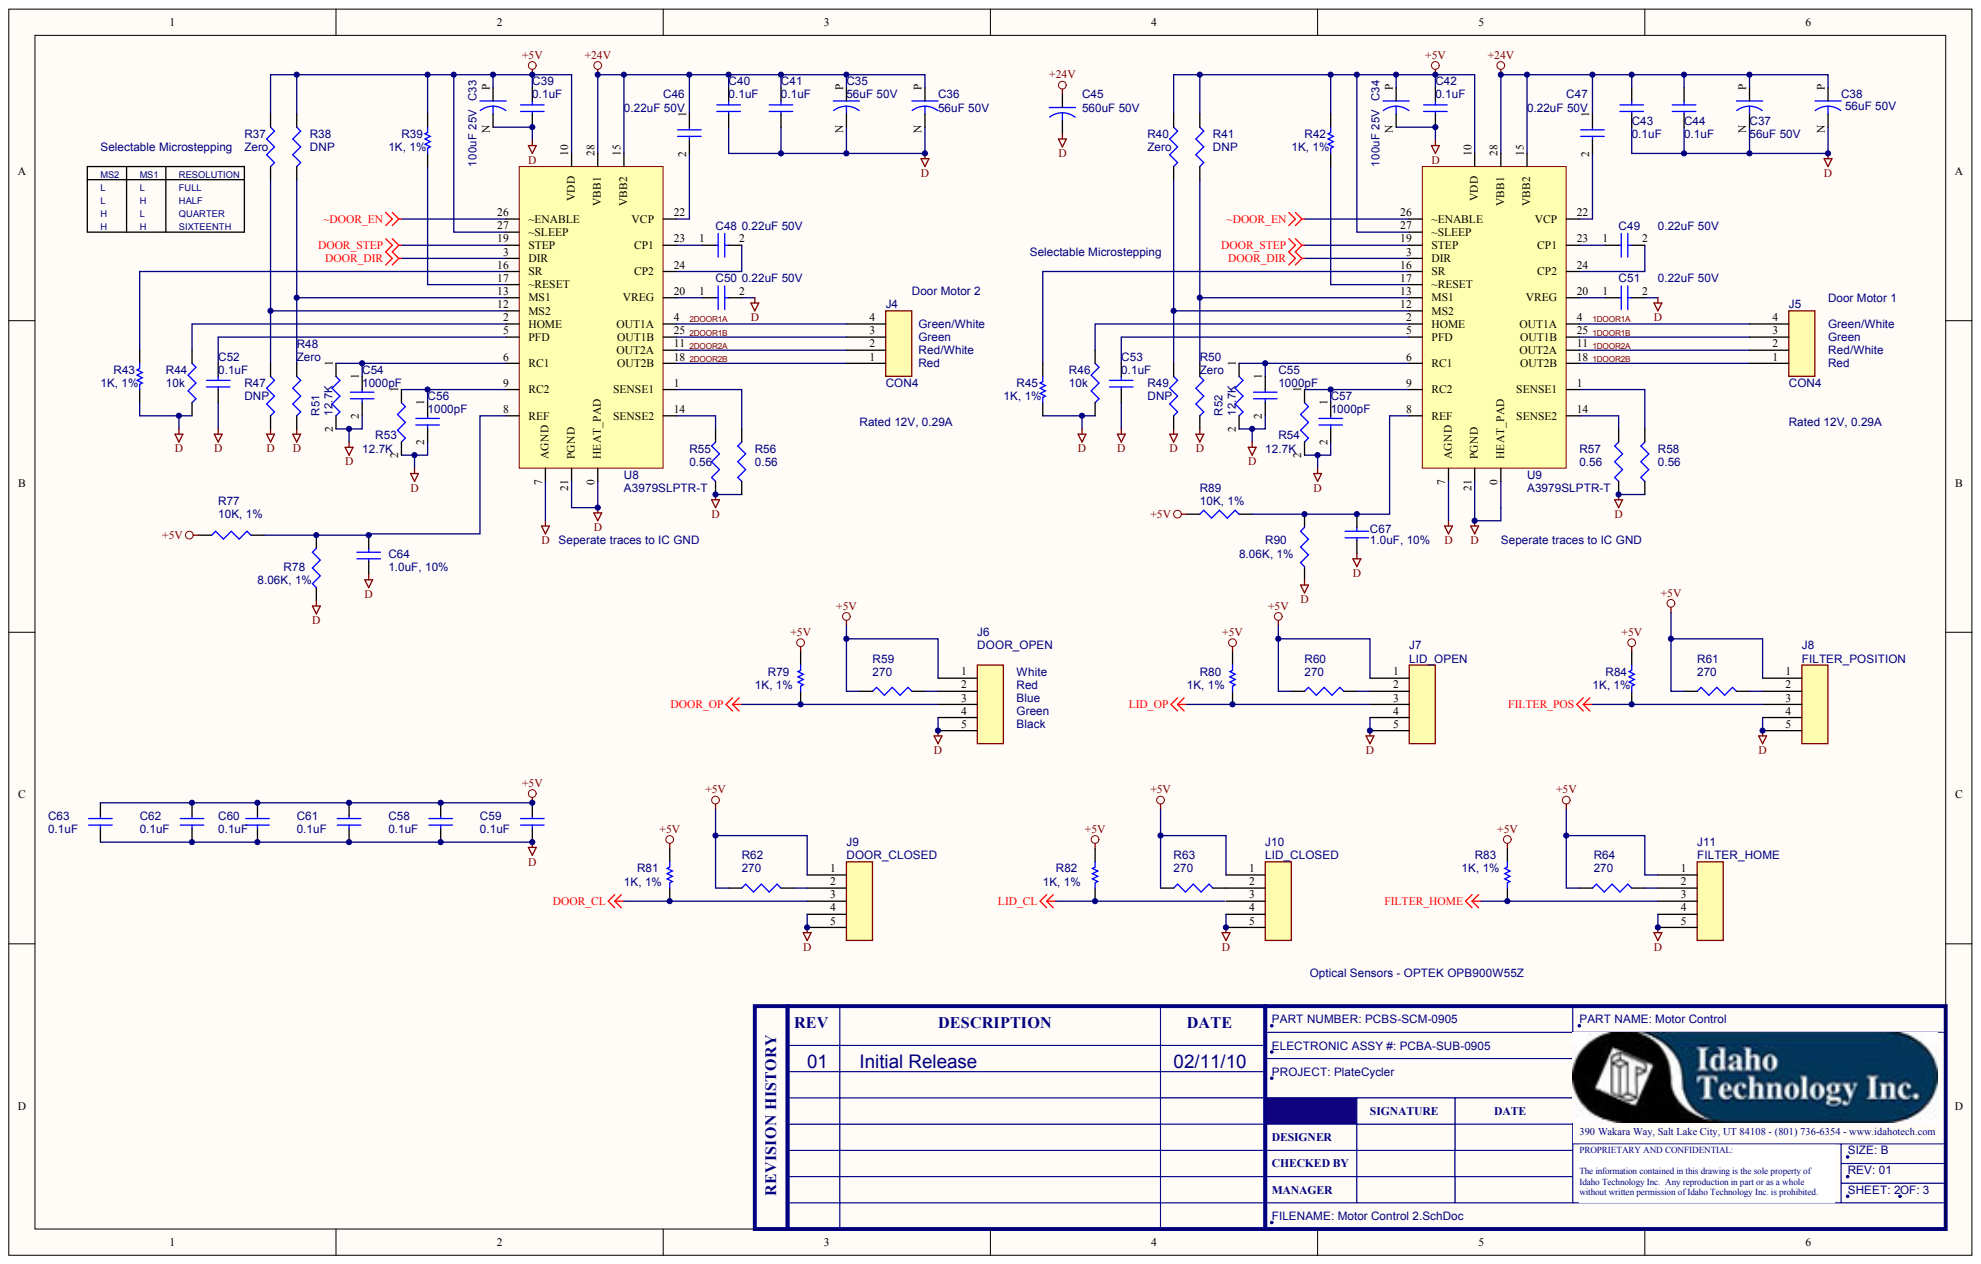
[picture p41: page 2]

Seperate traces to IC GND

REV | DESCRIPTION | DATE | PART NUMBER: PCBS-SCM-0905 | PART NAME: Motor Control

ELECTRONIC ASSY #: PCBA-SUB-0905 | 390 Wakara Way, Salt Lake City, UT 84108 - (801) 736-6354 - www.idahotech.com

SIGNATURE | DATE

DESIGNER

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

MANAGER

FILENAME: Motor Control 2.SchDoc

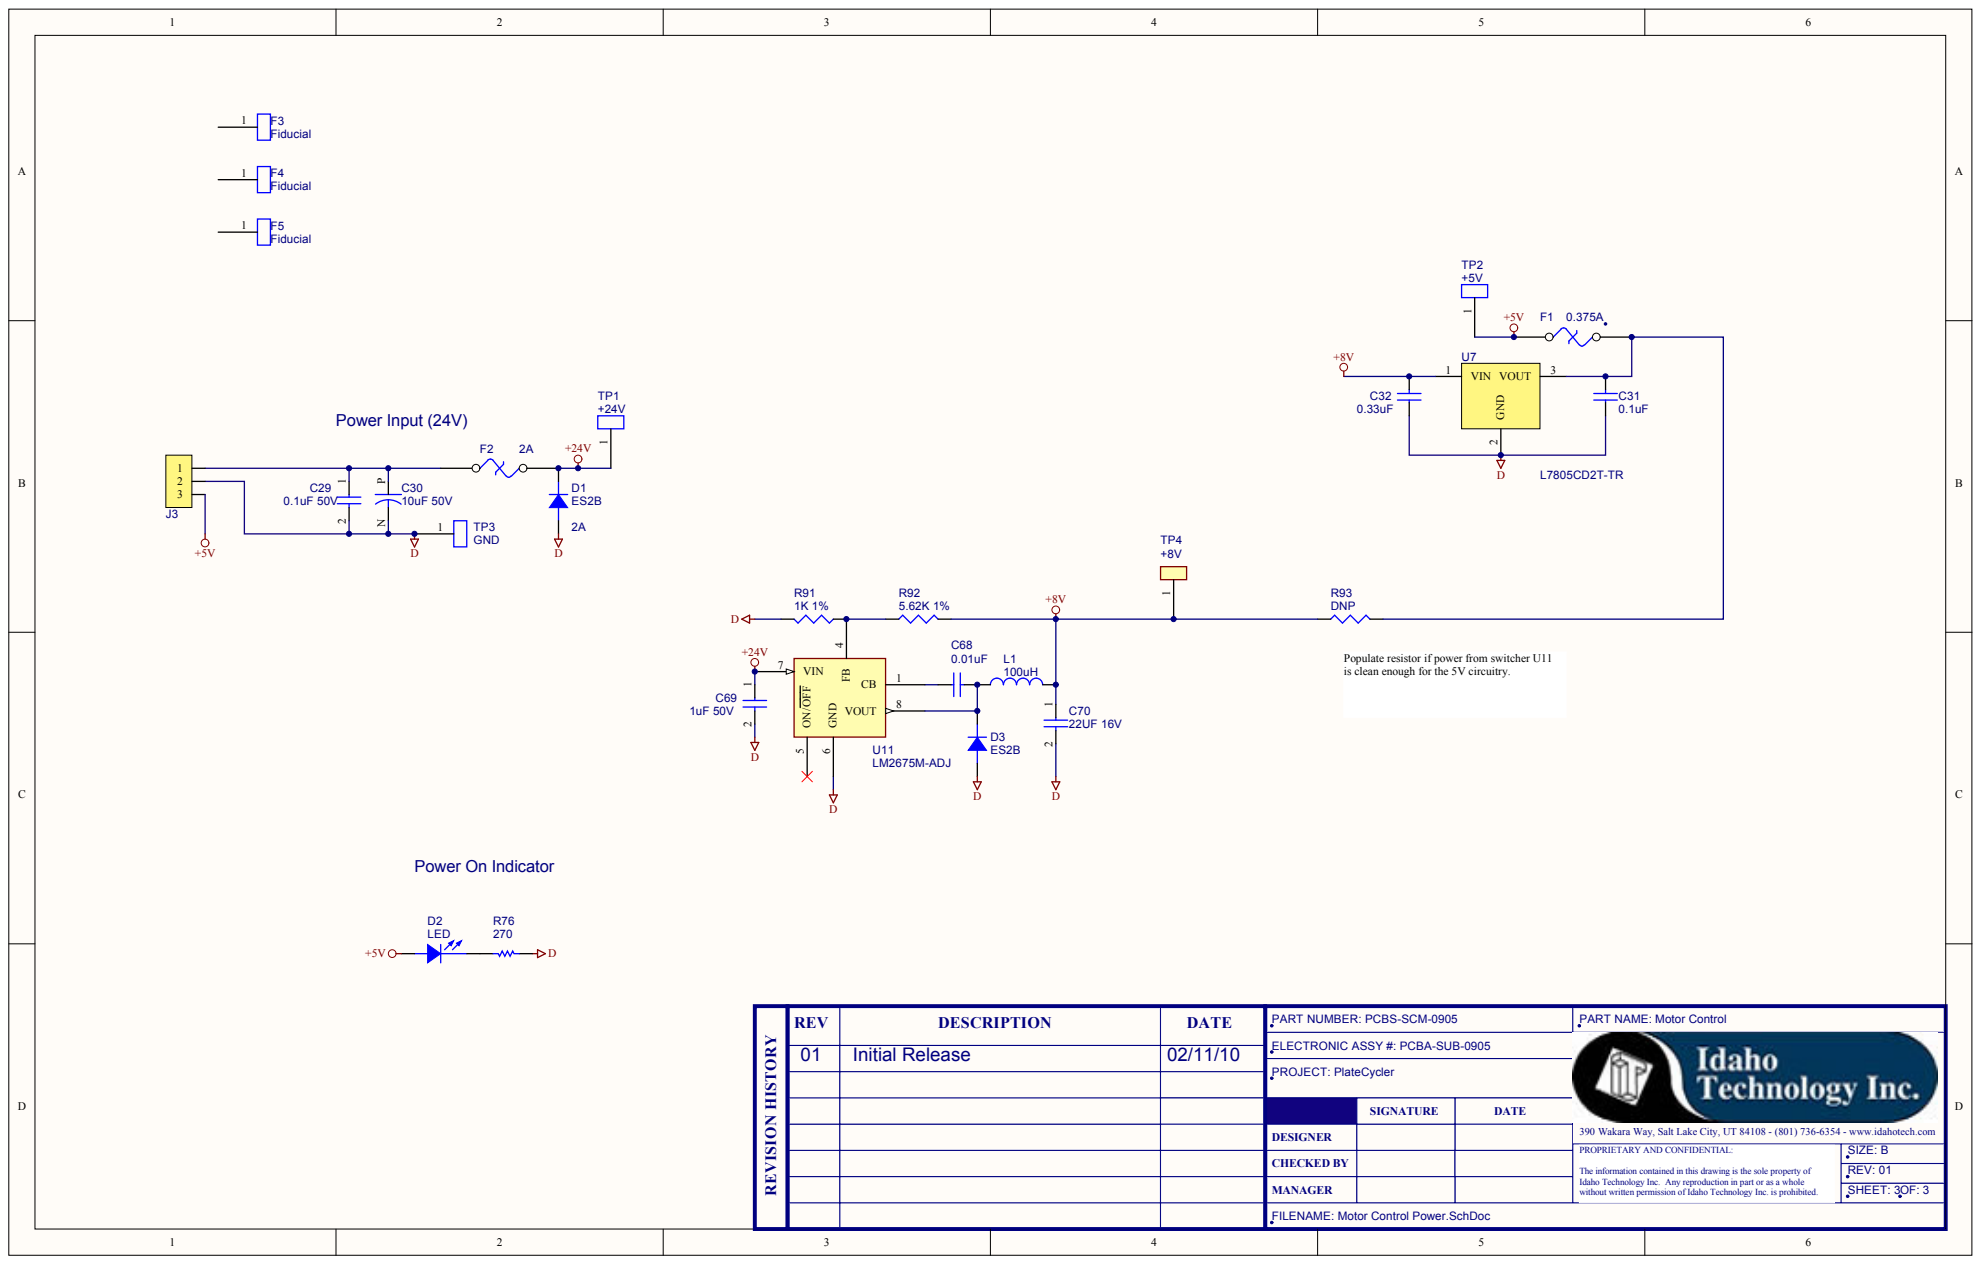
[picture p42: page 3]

Populate resistor if power from switcher U11
is clean enough for the 5V circuitry.

REV | DESCRIPTION | DATE | PART NUMBER: PCBS-SCM-0905 | PART NAME: Motor Control

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

SIGNATURE | DATE

DESIGNER

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

MANAGER

FILENAME: Motor Control Power.SchDoc

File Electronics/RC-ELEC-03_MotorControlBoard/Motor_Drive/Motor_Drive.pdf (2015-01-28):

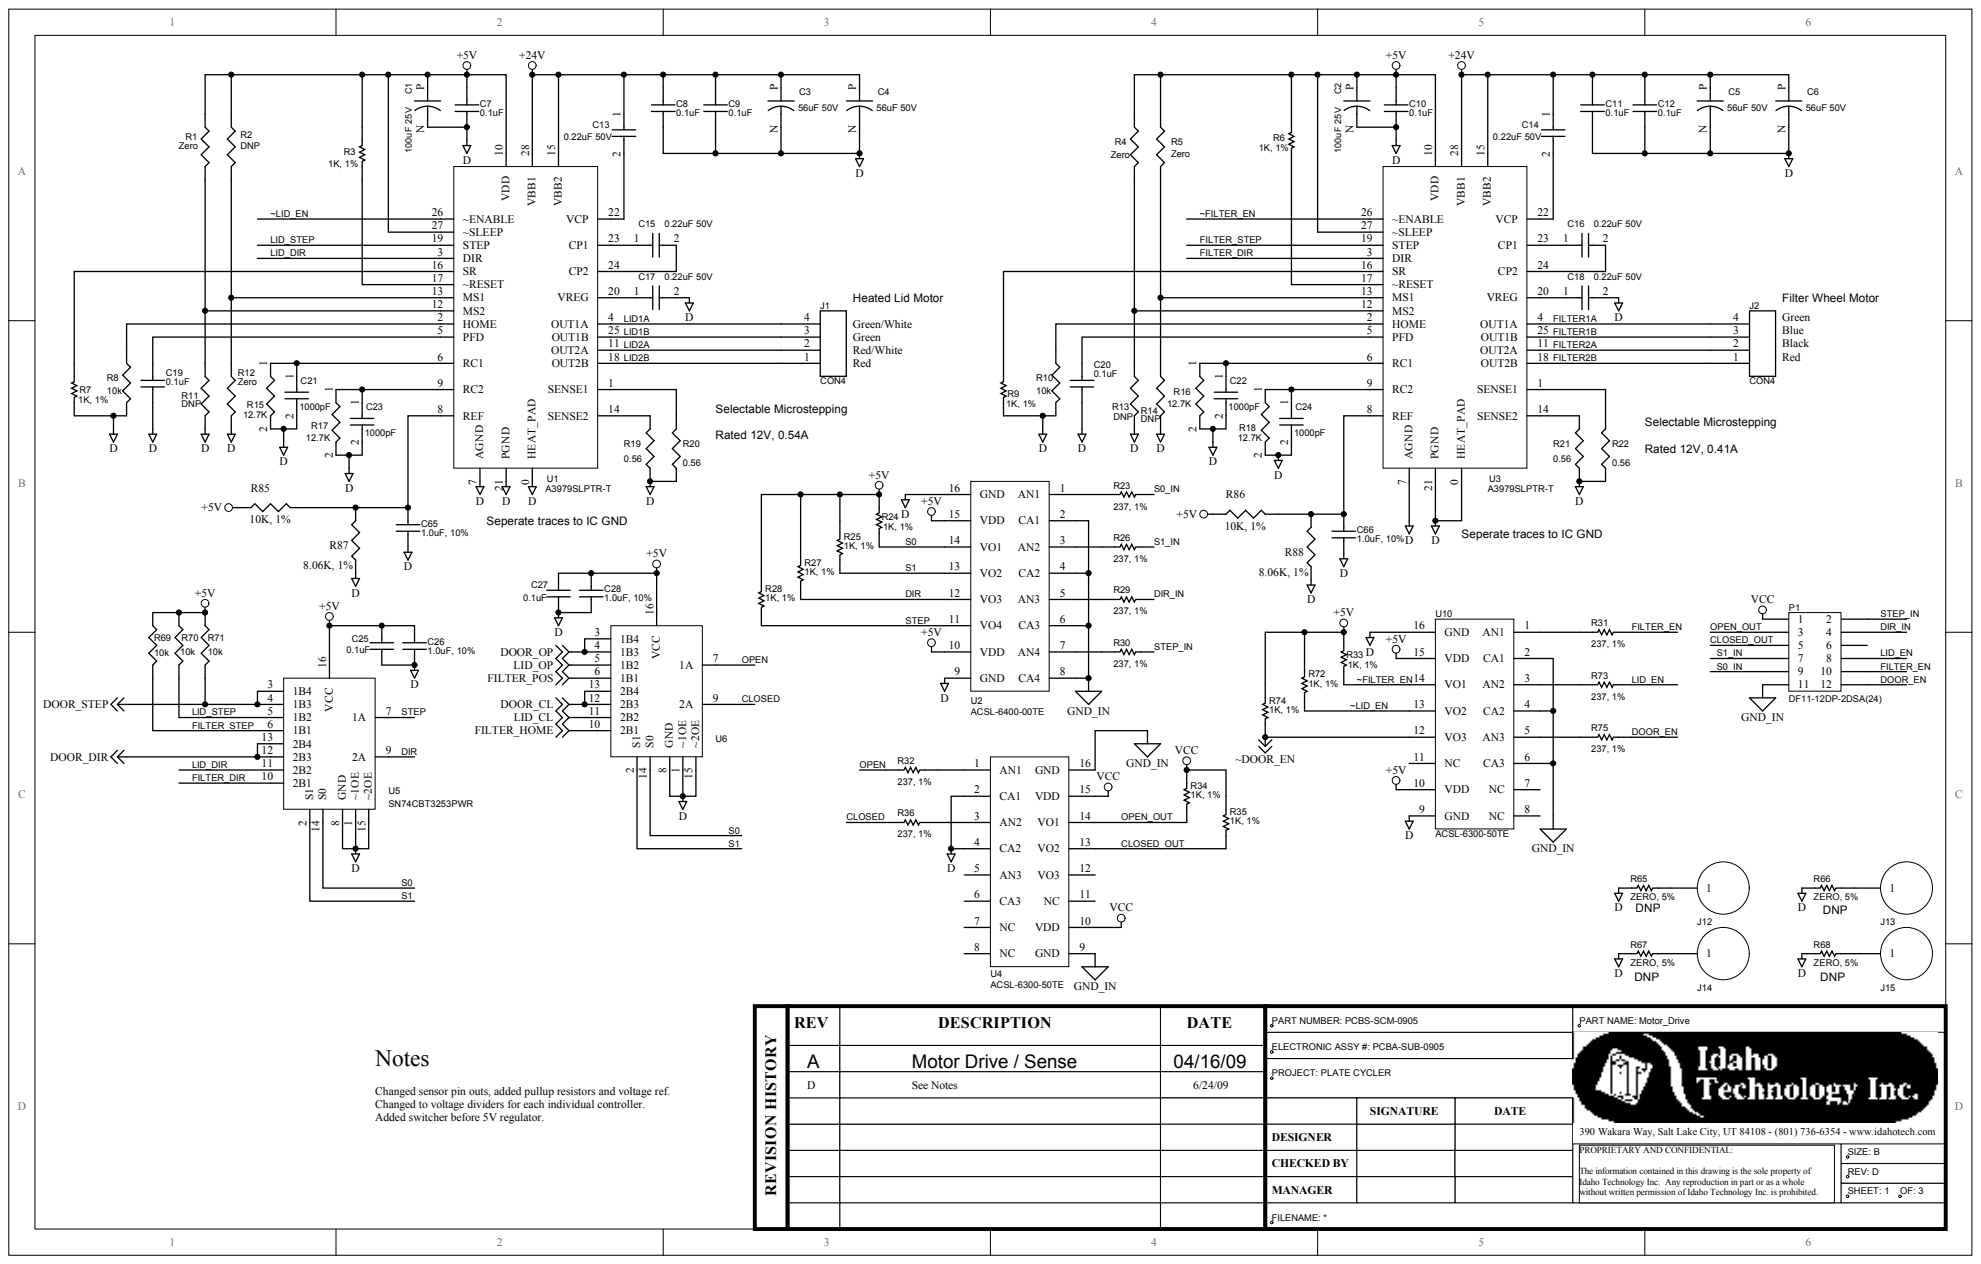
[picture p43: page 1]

Seperate traces to IC GND

REV | DESCRIPTION | DATE | PART NUMBER: PCBS-SCM-0905 | PART NAME: Motor_Drive

ELECTRONIC ASSY #: PCBA-SUB-0905 | 390 Wakara Way, Salt Lake City, UT 84108 - (801) 736-6354 - www.idahotech.com

A | Motor Drive / Sense | 04/16/09

D | See Notes Changed sensor pin outs, added pullup resistors and voltage ref. | 6/24/09

Changed to voltage dividers for each individual controller.
Added switcher before 5V regulator.

SIGNATURE | DATE

DESIGNER

The information contained in this drawing is the sole property of
Idaho Technology Inc. Any reproduction in part or as a whole

MANAGER

FILENAME: *

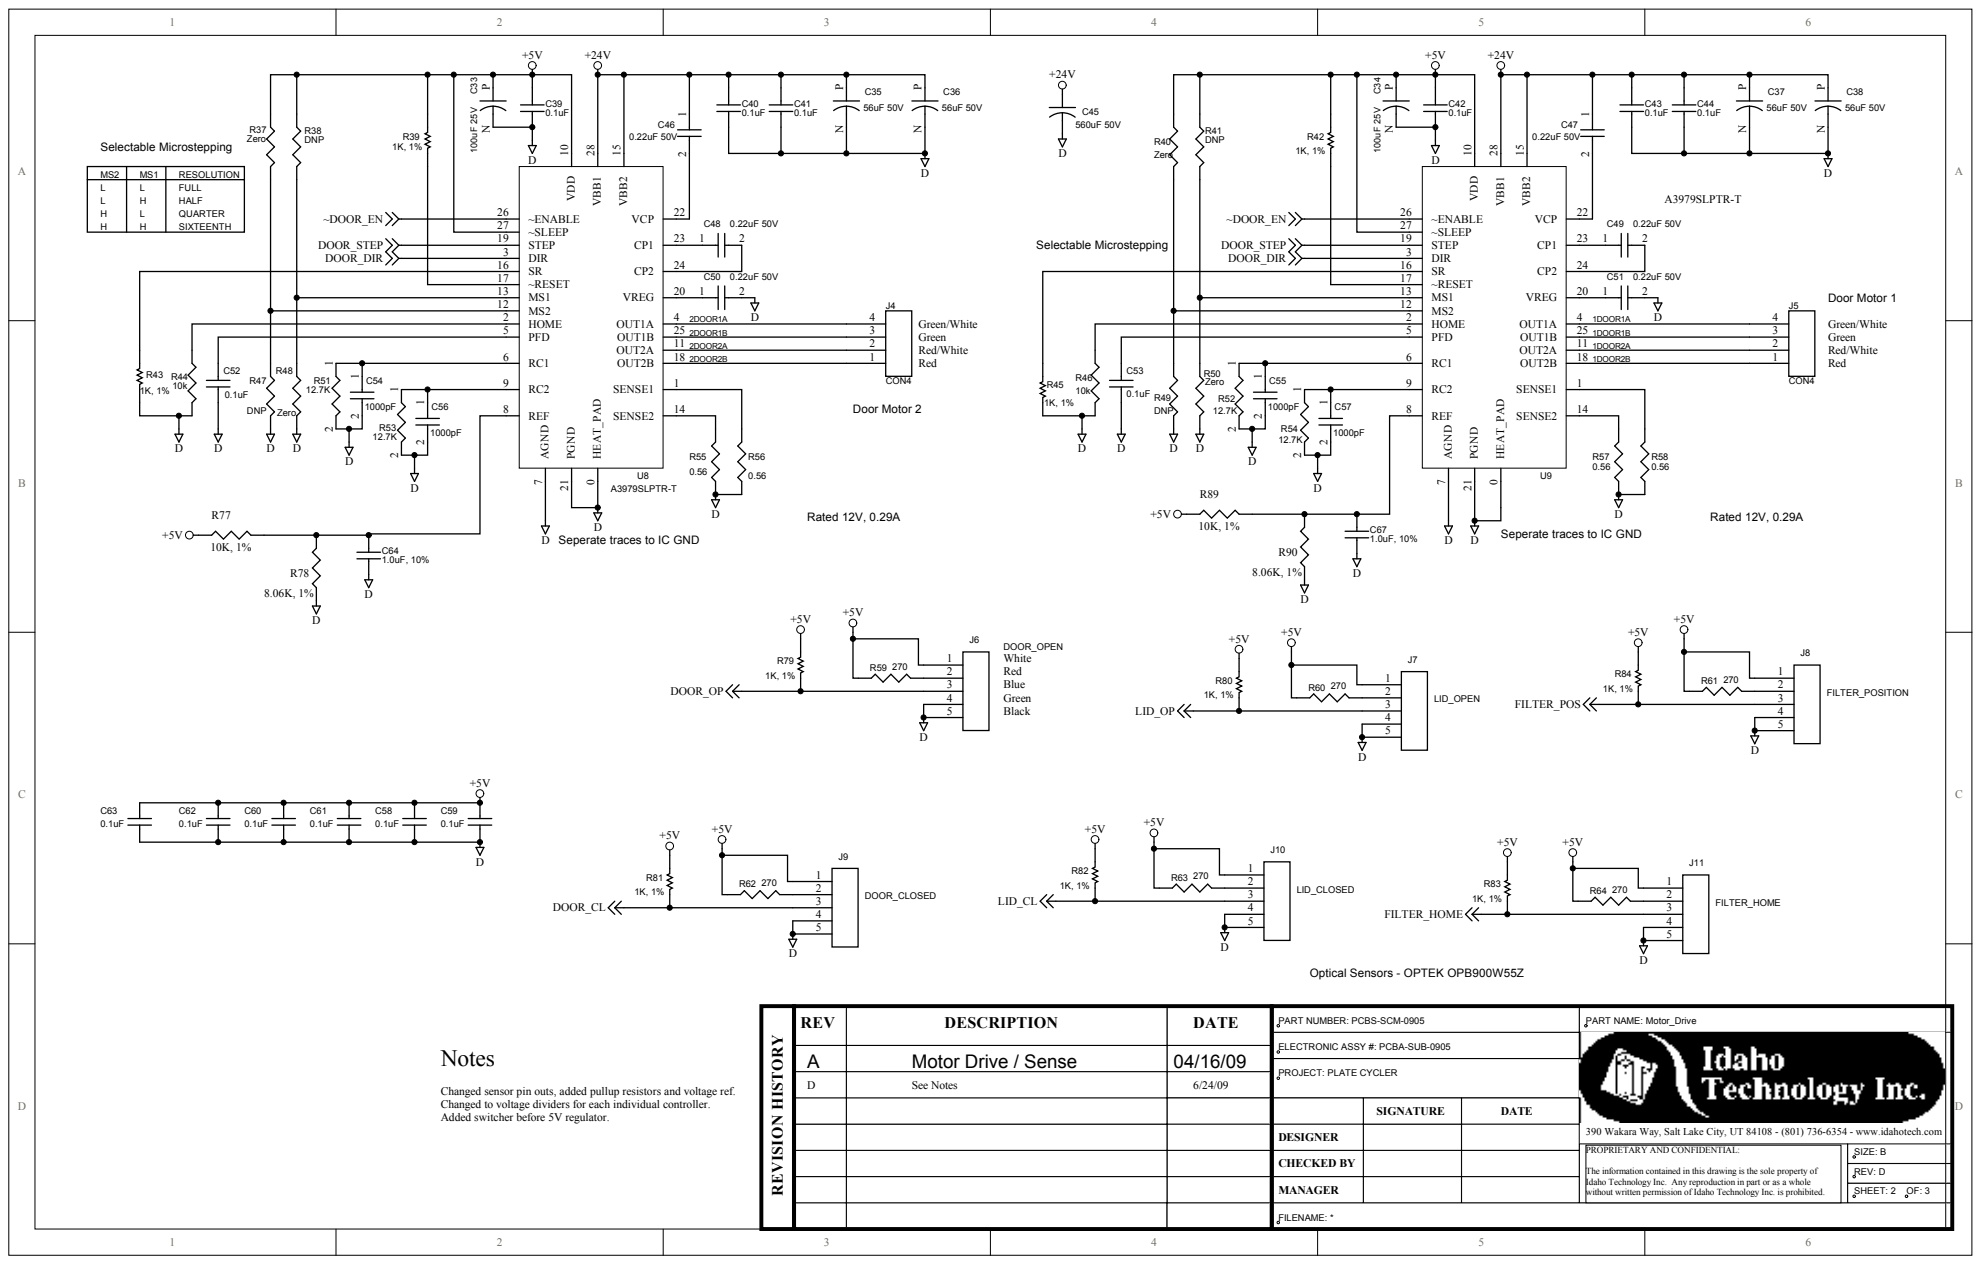
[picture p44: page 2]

Seperate traces to IC GND

REV | DESCRIPTION | DATE | PART NUMBER: PCBS-SCM-0905 | PART NAME: Motor_Drive

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

A | Motor Drive / Sense | 04/16/09

D | See Notes Changed sensor pin outs, added pullup resistors and voltage ref. | 6/24/09

Changed to voltage dividers for each individual controller.
Added switcher before 5V regulator.

SIGNATURE | DATE

DESIGNER

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

MANAGER

FILENAME: *

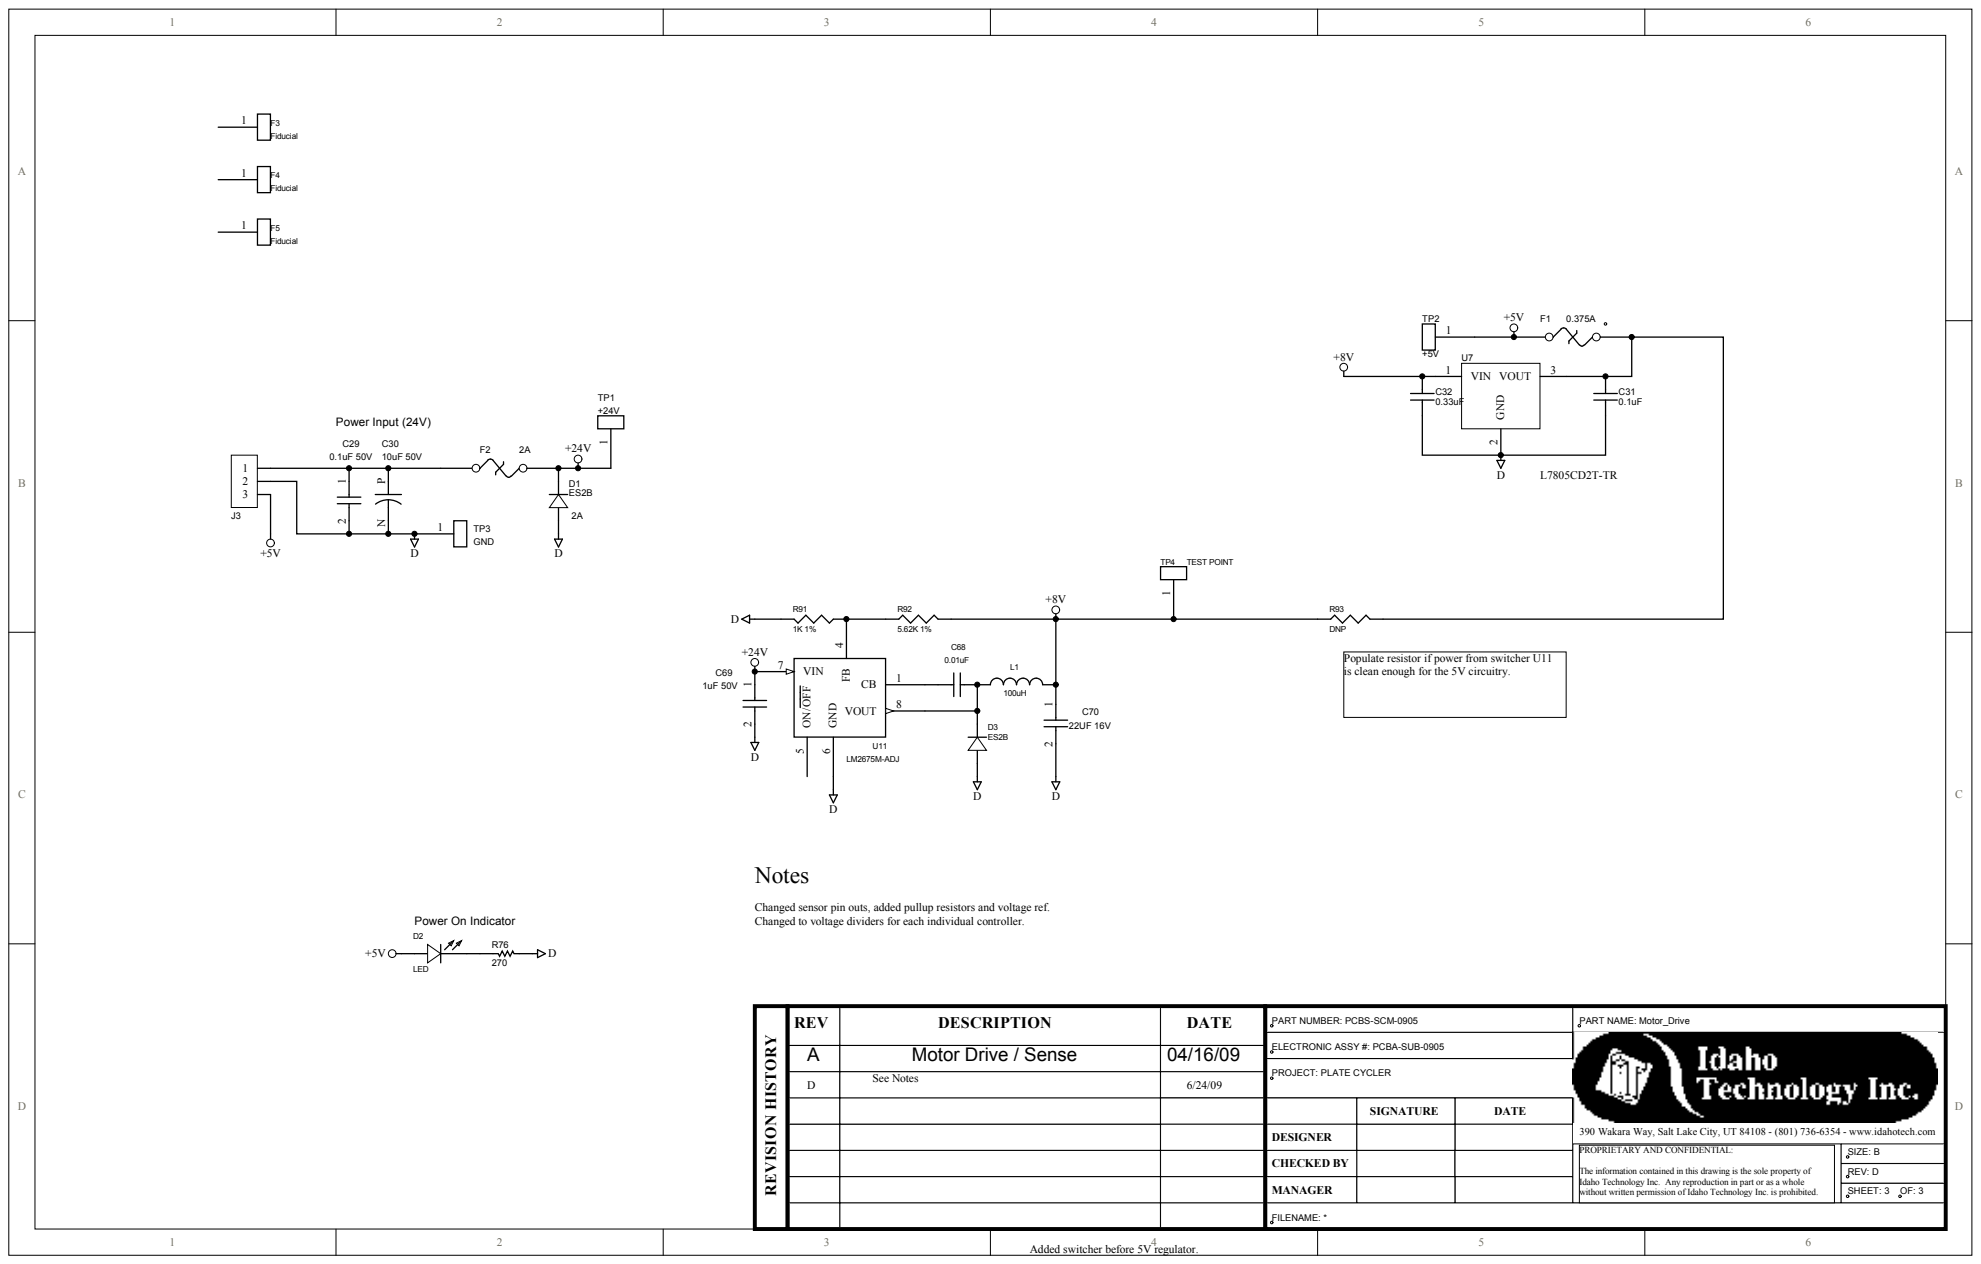
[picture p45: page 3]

Populate resistor if power from switcher U11
is clean enough for the 5V circuitry.

Changed sensor pin outs, added pullup resistors and voltage ref.
Changed to voltage dividers for each individual controller.

REV | DESCRIPTION | DATE | PART NUMBER: PCBS-SCM-0905 | PART NAME: Motor_Drive
A | Motor Drive / Sense | 04/16/09

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

D | See Notes | 6/24/09

SIGNATURE | DATE

DESIGNER

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

MANAGER

FILENAME: *

Added switcher before 5V regulator.

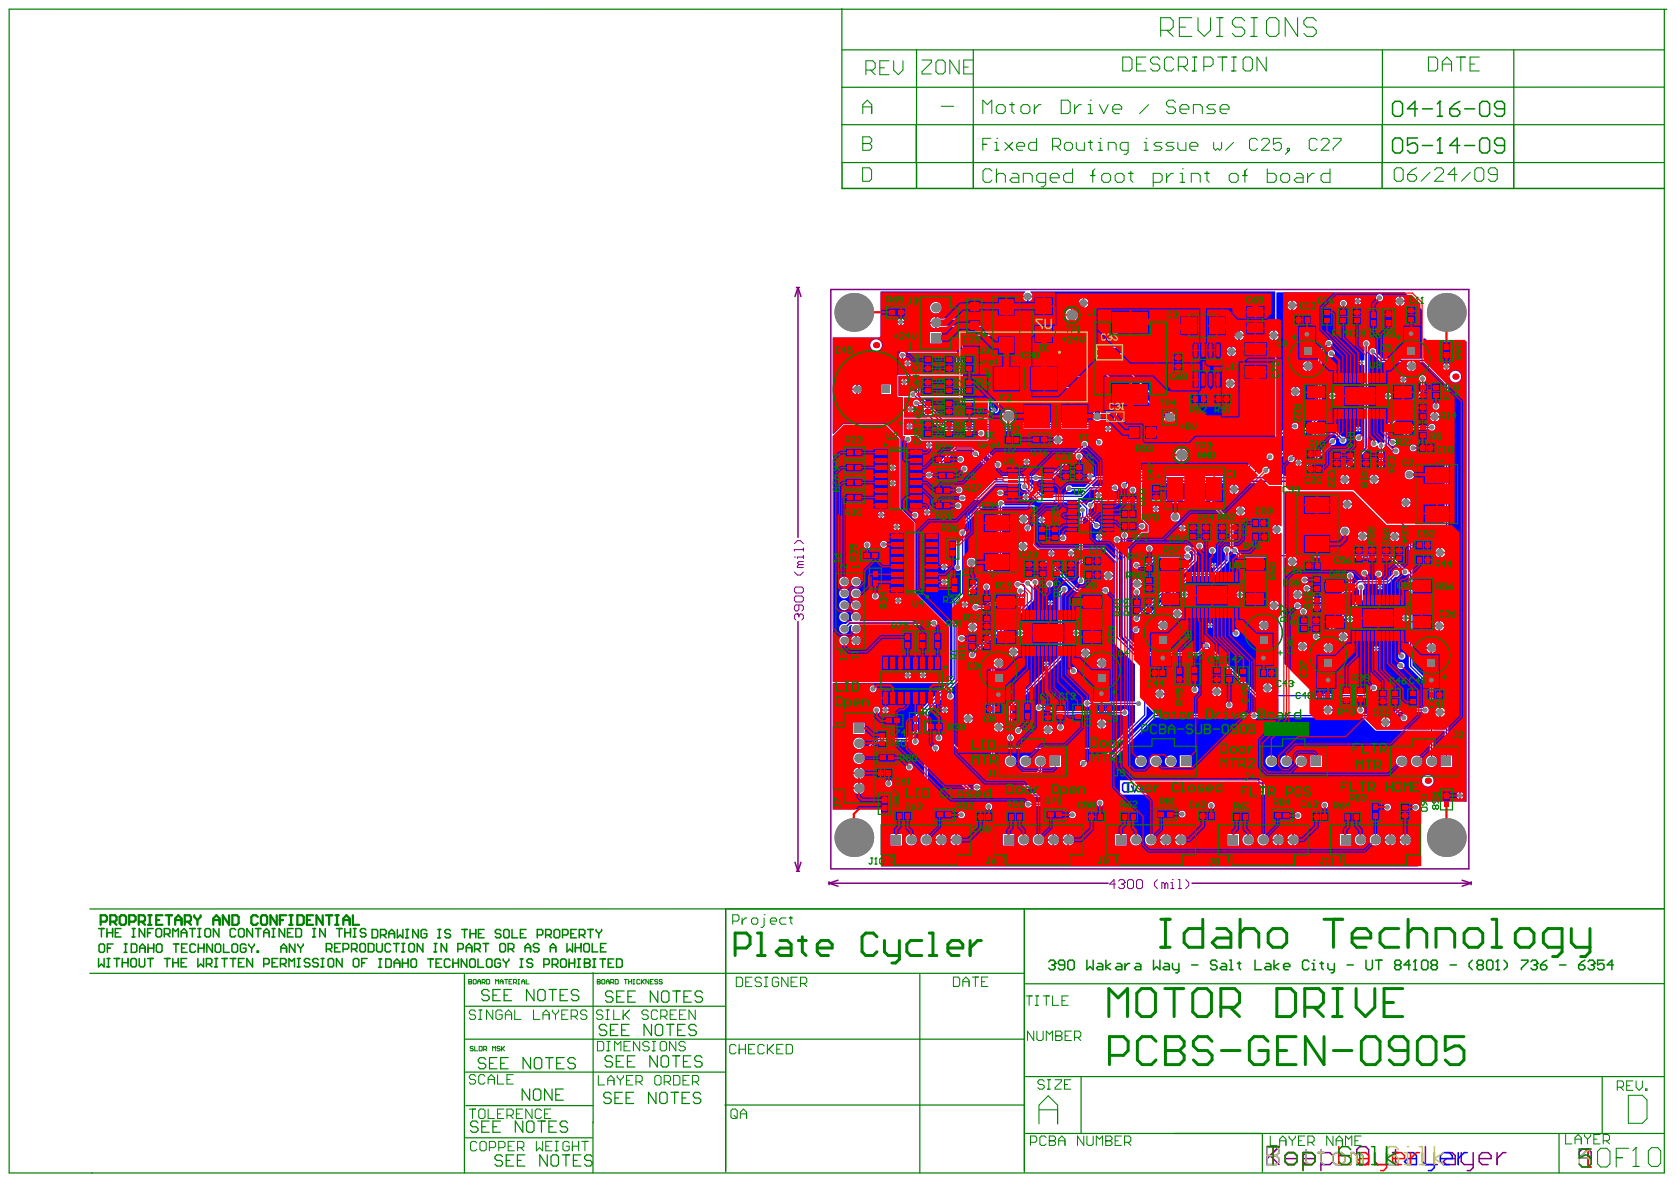
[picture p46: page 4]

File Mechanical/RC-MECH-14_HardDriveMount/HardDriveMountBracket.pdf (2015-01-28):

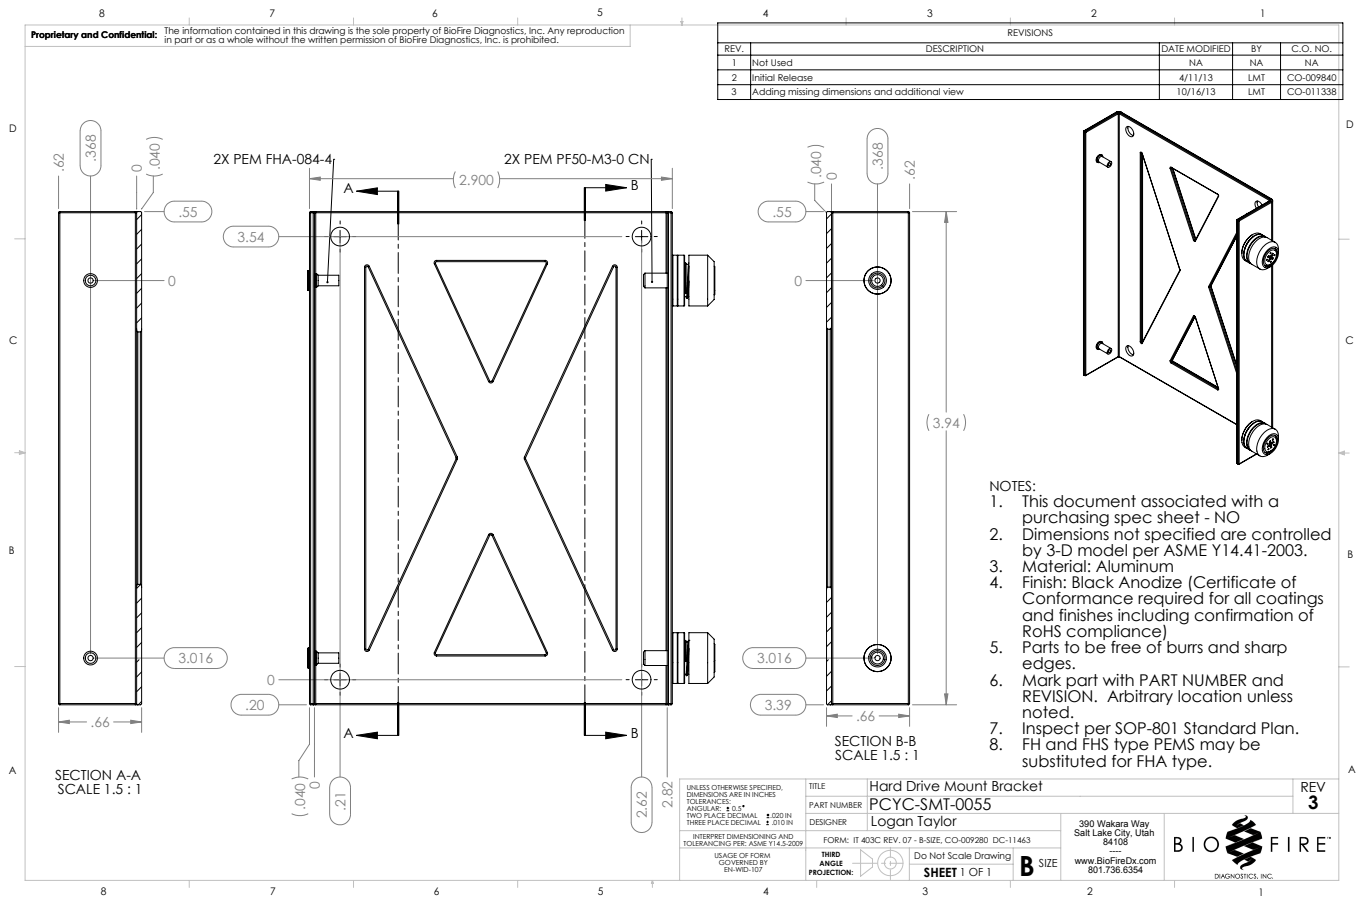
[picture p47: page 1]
2X PEM FHA-084-4; 2X PEM PF50-M3-0 CN; SECTION A-A SCALE 1.5 : 1; SECTION B-B SCALE 1.5 : 1; Hard Drive Mount Bracket; REV; Logan Taylor; SHEET 1 OF 1; B SIZE; TWO PLACE DECIMAL

The information contained in this drawing is the sole property of BioFire Diagnostics, Inc. Any reproduction

Proprietary and Confidential:
in part or as a whole without the written permission of BioFire Diagnostics, Inc. is prohibited. Proprietary and Confidential:

REV. | DESCRIPTION | DATE MODIFIED | BY | C.O. NO.
1 | Not Used | NA | NA | NA
2 | Initial Release | 4/11/13 | LMT | CO-009840
3 | Adding missing dimensions and additional view | 10/16/13 | LMT | CO-011338

NOTES:
1. This document associated with a
purchasing spec sheet - NO
2. Dimensions not specified are controlled
by 3-D model per ASME Y14.41-2003.
3. Material: Aluminum
4. Finish: Black Anodize (Certificate of
Conformance required for all coatings
and finishes including confirmation of
RoHS compliance)
5. Parts to be free of burrs and sharp
edges.
6. Mark part with PART NUMBER and
REVISION. Arbitrary location unless
noted.
7. Inspect per SOP-801 Standard Plan.
8. FH and FHS type PEMS may be
substituted for FHA type.

UNLESS OTHERWISE SPECIFIED,
DIMENSIONS ARE IN INCHES
TOLERANCES:
ANGULAR: 0.5
THREE PLACE DECIMAL .010 IN
INTERPRET DIMENSIONING AND
TOLERANCING PER: ASME Y14.5-2009

TITLE
PART NUMBER
DESIGNER
FORM: IT 403C REV. 07 - B-SIZE, CO-009280 DC-11463
THIRD
ANGLE
PROJECTION:

390 Wakara Way
Salt Lake City, Utah
www.BioFireDx.com

USAGE OF FORM
GOVERNED BY
EN-WID-107

Do Not Scale Drawing

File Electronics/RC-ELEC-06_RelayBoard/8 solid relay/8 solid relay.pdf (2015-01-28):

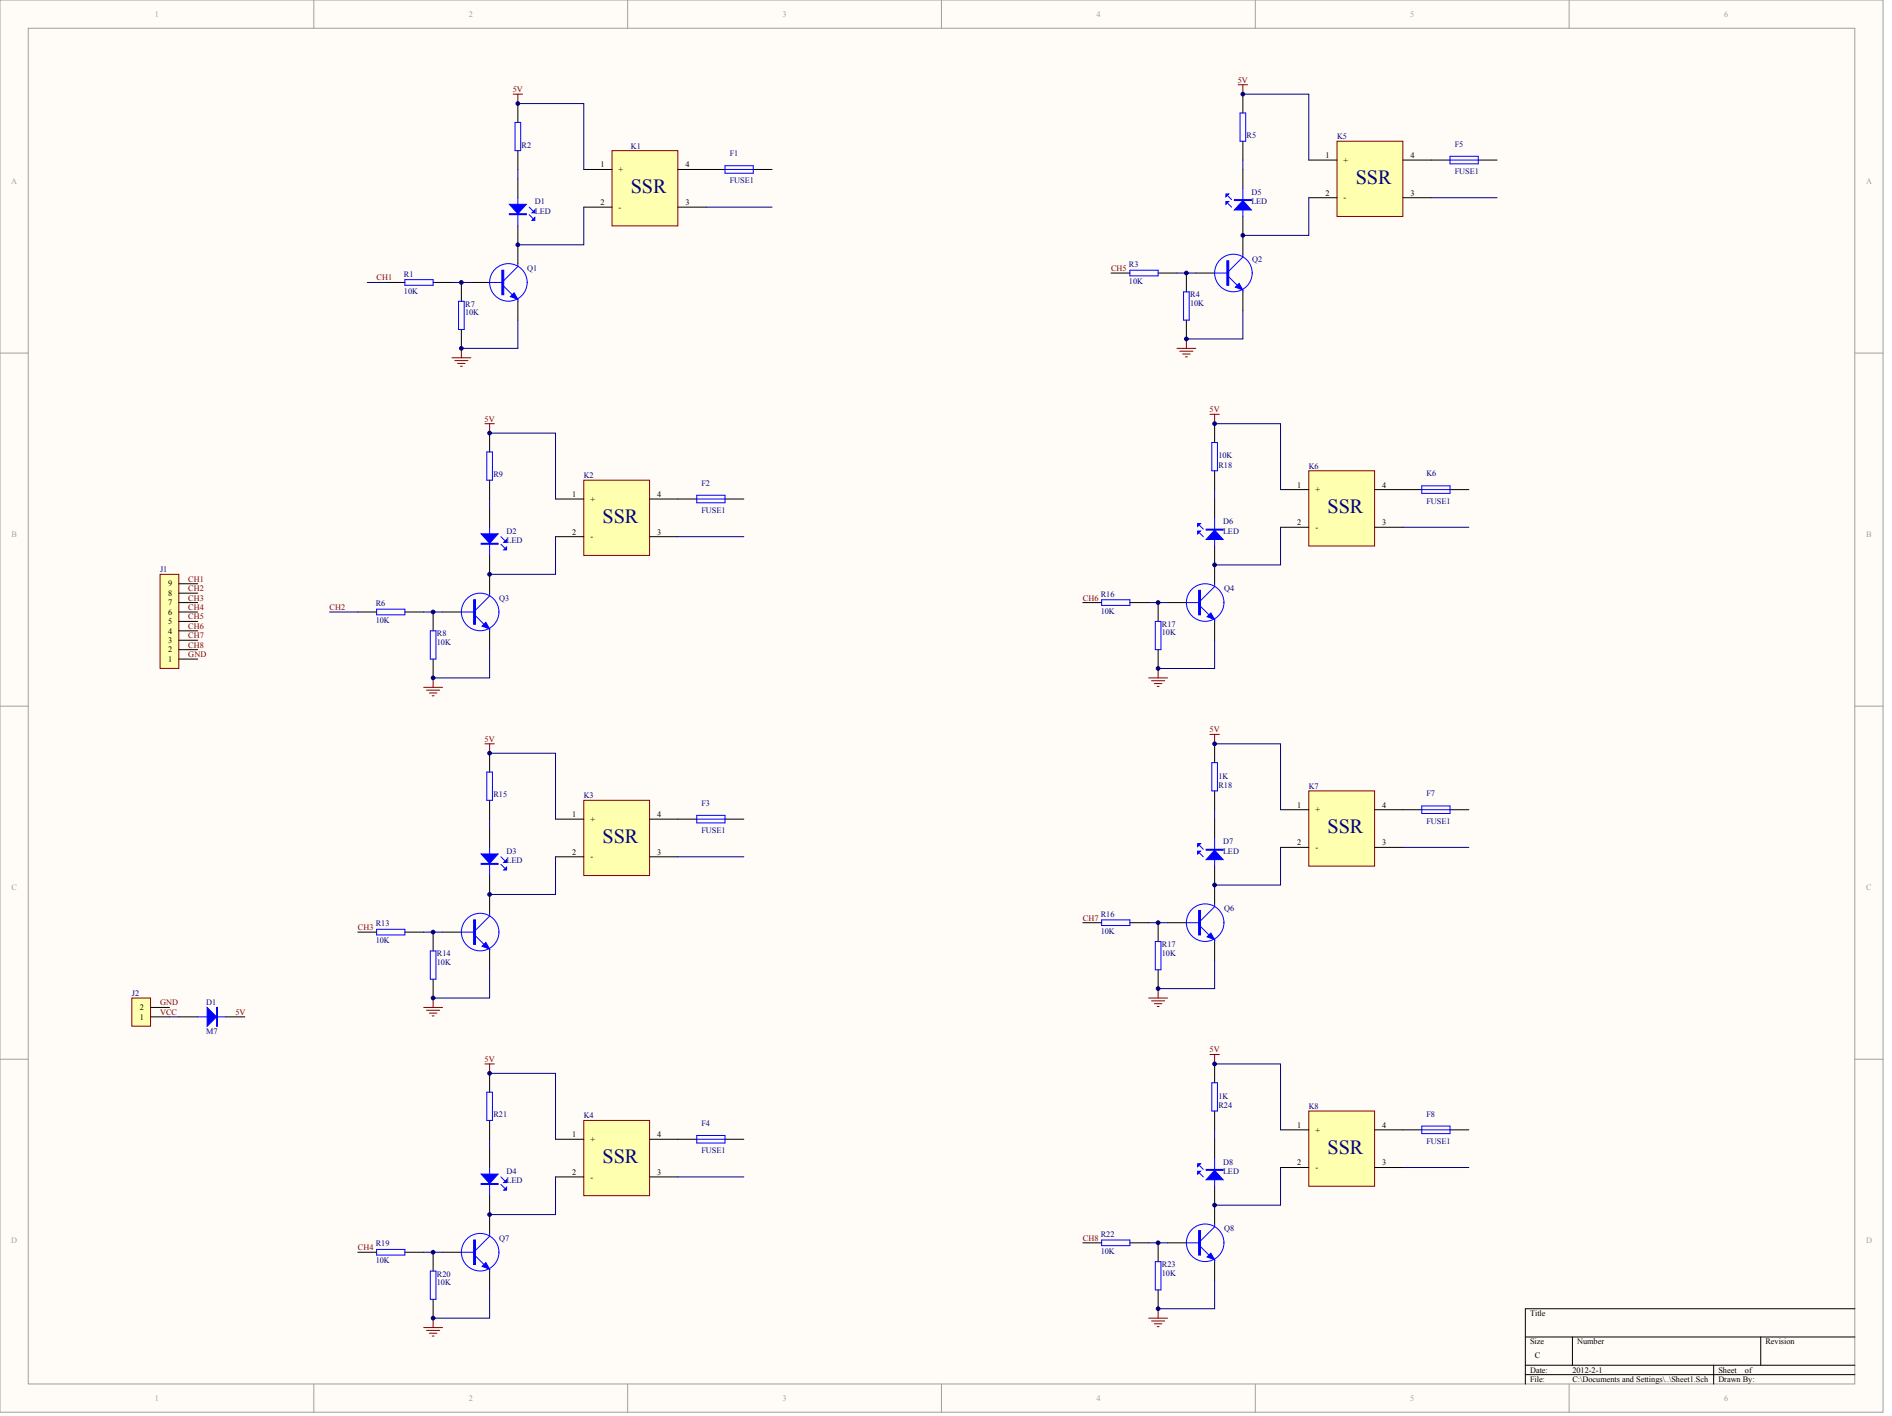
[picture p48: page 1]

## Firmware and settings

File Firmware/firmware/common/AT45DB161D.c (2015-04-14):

/////////////////////////////////////////////////////////////
//
//  AT45DB161D.c
//
//  Atmel AT45DB161D Driver
//

#include <AT45DB161D.h>
#include <spi.h>
#include <xparameters.h>
#include <processor.h>
#include <assert.h>
#include <string.h>
#include <stdio.h>
#include <ctype.h>



///////////////////////////////////////////////////
// Constants

enum OpCodes
{
    OP_BLOCK_ERASE                           = 0x50,
    OP_MAIN_MEMORY_PAGE_READ                 = 0xD2,
    OP_CONTINUOUS_ARRAY_READ_LOW_SPEED       = 0x03,
    OP_CONTINUOUS_ARRAY_READ_HIGH_SPEED      = 0x0B,
    OP_BUFFER1_READ_LOW_SPEED                = 0xD1,
    OP_BUFFER2_READ_LOW_SPEED                = 0xD3,
    OP_BUFFER1_READ_LOW                      = 0xD4,
    OP_BUFFER2_READ_LOW                      = 0xD6,
    
    OP_BUFFER1_WRITE                         = 0x84,
    OP_BUFFER2_WRITE                         = 0x87,
    OP_BUFFER1_TO_PAGE_PROG_WITH_ERASE       = 0x83,
    OP_BUFFER2_TO_PAGE_PROG_WITH_ERASE       = 0x86,
    
    OP_STATUS_REGISTER_READ                  = 0xD7,
};



#define TX_TIMEOUT_us         10000
#define RX_TIMEOUT_us         10000

#define MAX_SINGLE_READ_SIZE          (SPI_BUFFER_SIZE - 5)
#define MAX_SINGLE_BUFFER_WRITE_SIZE  (SPI_BUFFER_SIZE - 4)



///////////////////////////////////////////////////
// Local types and macros



///////////////////////////////////////////////////
// Local function prototypes

static bool sendAndReceiveSpiData(SpiInterface* spiInterface, uint8* writeBuffer, uint8* readBuffer, uint16 count);
static bool singleRead(SpiInterface* spiInterface, uint32 addr, uint8* buffer, uint32 count);
static bool pageWrite(SpiInterface* spiInterface, uint32 pageNumber, uint8* buffer);
static bool buffer1Write(SpiInterface* spiInterface, uint32 addr, uint8* buffer, uint32 count);
static bool writeBuffer1toPage(SpiInterface* spiInterface, uint32 pageNumber);

static bool isReady(SpiInterface* spiInterface);

static void loadAddrBytesWithAddr(uint8* buffer, uint32 addr);
static void loadAddrBytesWithPage(uint8* buffer, uint32 page);

void dispData(uint8* buf, uint32 count);



///////////////////////////////////////////////////
// Local data

SpiInterface spiInterfaceSoftwareFlash;
SpiInterface spiInterfacePlatformFlash;



///////////////////////////////////////////////////
// Interface functions

void serialFlashInit()
{
    spiInterfaceInit(&spiInterfacePlatformFlash, XPAR_CONFIG_FLASH_SPI_DEVICE_ID,
                     XPAR_INTC_CONFIG_FLASH_SPI_IP2INTC_IRPT_INTR,
                     XSP_MASTER_OPTION | XSP_MANUAL_SSELECT_OPTION | XSP_CLK_ACTIVE_LOW_OPTION | XSP_CLK_PHASE_1_OPTION,
                     0);

    spiInterfaceInit(&spiInterfaceSoftwareFlash, XPAR_USER_FLASH_SPI_DEVICE_ID,
                     XPAR_INTC_USER_FLASH_SPI_IP2INTC_IRPT_INTR,
                     XSP_MASTER_OPTION | XSP_MANUAL_SSELECT_OPTION | XSP_CLK_ACTIVE_LOW_OPTION | XSP_CLK_PHASE_1_OPTION,
                     0);
}


uint8 readStatusRegister(SpiInterface* spiInterface)
{
    uint8 writeBuffer[SPI_BUFFER_SIZE];
    uint8 readBuffer[SPI_BUFFER_SIZE];

    writeBuffer[0] = OP_STATUS_REGISTER_READ;
    writeBuffer[1] = 0x00;

    if(!sendAndReceiveSpiData(spiInterface, writeBuffer, readBuffer, 2)) return 0;

    return readBuffer[1];
}



bool eraseFlashBlock(uint32 blockNumber)
{
    ASSERT(blockNumber < FLASH_BLOCK_COUNT);

    while(!isReady(&spiInterfaceSoftwareFlash))
    { ; }

    uint8 writeBuffer[SPI_BUFFER_SIZE];
    uint8 readBuffer[SPI_BUFFER_SIZE];

    writeBuffer[0] = OP_BLOCK_ERASE;
    writeBuffer[1] = blockNumber >> 3;
    writeBuffer[2] = 0x000000ff & (blockNumber << 5);
    writeBuffer[3] = 0x00;

    return sendAndReceiveSpiData(&spiInterfaceSoftwareFlash, writeBuffer, readBuffer, 4);
}




bool readFlash(uint32 addr, uint8* buffer, uint32 count)
{
    ASSERT(buffer);

    while(!isReady(&spiInterfaceSoftwareFlash))
    { ; }

    while(count > 0)
    {
        uint32 readCount = MIN(count, MAX_SINGLE_READ_SIZE);

        if(!singleRead(&spiInterfaceSoftwareFlash, addr, buffer, readCount)) return false;
        
        buffer += readCount;
        addr   += readCount;
        count  -= readCount;
    }

    return true;
}



bool writeFlash(uint32 addr, uint8* buffer, uint32 count)
{
    ASSERT(buffer);

    while(count > 0)
    {
        uint32 page       = addr / FLASH_PAGE_SIZE;
        uint32 pageOffset = addr % FLASH_PAGE_SIZE;
        uint32 writeCount = MIN(count, FLASH_PAGE_SIZE - pageOffset);
        uint8  writeBuffer[FLASH_PAGE_SIZE];

        if(writeCount < FLASH_PAGE_SIZE)
        {
            memset(writeBuffer, 0xff, sizeof(writeBuffer));
            memcpy(&writeBuffer[pageOffset], buffer, writeCount);

            if(!pageWrite(&spiInterfaceSoftwareFlash, page, writeBuffer)) return false;
        }
        else
        {
            if(!pageWrite(&spiInterfaceSoftwareFlash, page, buffer)) return false;
        }

        buffer += writeCount;
        addr   += writeCount;
        count  -= writeCount;
    }

    return true;
}



#ifndef BOOTLOADER

bool readPlatformFlash(uint32 addr, uint8* buffer, uint32 count)
{
    ASSERT(buffer);

    while(!isReady(&spiInterfacePlatformFlash))
    { ; }

    while(count > 0)
    {
        uint32 readCount = MIN(count, MAX_SINGLE_READ_SIZE);

        if(!singleRead(&spiInterfacePlatformFlash, addr, buffer, readCount)) return false;
        
        buffer += readCount;
        addr   += readCount;
        count  -= readCount;
    }

    return true;
}



bool writePlatformFlash(uint32 addr, uint8* buffer, uint32 count)
{
    ASSERT(buffer);

    while(count > 0)
    {
        uint32 page       = addr / FLASH_PAGE_SIZE;
        uint32 pageOffset = addr % FLASH_PAGE_SIZE;
        uint32 writeCount = MIN(count, FLASH_PAGE_SIZE - pageOffset);
        uint8  writeBuffer[FLASH_PAGE_SIZE];

        if(writeCount < FLASH_PAGE_SIZE)
        {
            memset(writeBuffer, 0xff, sizeof(writeBuffer));
            memcpy(&writeBuffer[pageOffset], buffer, writeCount);

            if(!pageWrite(&spiInterfacePlatformFlash, page, writeBuffer)) return false;
        }
        else
        {
            if(!pageWrite(&spiInterfacePlatformFlash, page, buffer)) return false;
        }

        buffer += writeCount;
        addr   += writeCount;
        count  -= writeCount;
    }

    return true;
}

#endif


///////////////////////////////////////////////////
// Local functions
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

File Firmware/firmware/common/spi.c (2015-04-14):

/////////////////////////////////////////////////////////////
//
//  spi.c
//
//  SPI Driver
//

#include <spi.h>
#include <xparameters.h>
#include <processor.h>
#include <assert.h>
#include <interrupt.h>
#include <string.h>
#include <timer.h>



///////////////////////////////////////////////////
// Constants


///////////////////////////////////////////////////
// Local types and macros



//////////////////////////////////////////////////
// Local function prototypes

static void dataCopy(SpiInterface* interface, uint8* toBuf, uint8* fromBuf, uint32 count);

static void spiInterruptHandler(void *callBackRef, Xuint32 statusEvent, Xuint32 byteCount);



///////////////////////////////////////////////////
// Local data



///////////////////////////////////////////////////
// Interface functions

void spiInterfaceInit(SpiInterface* interface, uint16 deviceId, uint8 interruptId, uint32 xilOptions, uint32 options)
{
    ASSERT(interface);
    
    interface->state            = SPI_STATE_IDLE;
    interface->invertedDataCopy = !!(options & SPI_INVERTED_DATA);

    XStatus status;

    status = XSpi_Initialize(&interface->hwInterface, deviceId);
    ASSERT(status == XST_SUCCESS);

    status = XSpi_SelfTest(&interface->hwInterface);
    ASSERT(status == XST_SUCCESS);

    status = XSpi_SetOptions(&interface->hwInterface, xilOptions);

    ASSERT(status == XST_SUCCESS);

    status = XSpi_SetSlaveSelect(&interface->hwInterface, 0);
    ASSERT(status == XST_SUCCESS);

 
    XSpi_SetStatusHandler(&interface->hwInterface, interface, (XSpi_StatusHandler)spiInterruptHandler);

    registerInterruptHandler(interruptId, (XInterruptHandler)XSpi_InterruptHandler, interface);
    enableInterrupt(interruptId);

    XSpi_Start(&interface->hwInterface);

    // \todo: Figure out why we have to do this!
    // Enable the first slave.
    XSpi_SetSlaveSelect(&interface->hwInterface, 0x01);
}



bool spiWaitForIdle(SpiInterface* interface, uint32 timeout_us)
{
    ASSERT(interface);

    Timer timer;
    
    startTimer(&timer, USEC_TO_TICKS(timeout_us));
    
    while(1)
    {
        SpiState state;
        
        CRData crdata = enterCriticalRegion();
        {
            state = interface->state;
        }
        exitCriticalRegion(crdata);

        if(state == SPI_STATE_IDLE || state == SPI_STATE_DONE || state == SPI_STATE_DONE_WITH_ERRORS)
        {
            return true;
        }
        else if(timerExpired(&timer))
        {
            return false;
        }
    }
    
    return false;
}



bool spiWaitForReady(SpiInterface* interface, uint32 timeout_us)
{
    ASSERT(interface);

    Timer timer;
    
    startTimer(&timer, USEC_TO_TICKS(timeout_us));
    
    while(1)
    {
        SpiState state;
        
        CRData crdata = enterCriticalRegion();
        {
            state = interface->state;
        }
        exitCriticalRegion(crdata);

        if(state == SPI_STATE_DONE || state == SPI_STATE_DONE_WITH_ERRORS)
        {
            return true;
        }
        else if(timerExpired(&timer))
        {
            return false;
        }
    }
    
    return false;
}



SpiStatus spiStartTransmit(SpiInterface* interface, uint8* writeBuffer, uint16 writeLength)
{
    SpiStatus status;
    
    ASSERT(interface);
    ASSERT(writeBuffer);
    ASSERT(writeLength <= SPI_BUFFER_SIZE);

    CRData crdata = enterCriticalRegion();
    {
        if(interface->state == SPI_STATE_TRANSMITTING)
        {
            status = SPI_STATUS_ERROR_TX_IN_PROCESS;
        }
        else
        {
            dataCopy(interface, interface->writeBuffer, writeBuffer, writeLength);
            interface->writeLength = writeLength;
            interface->state       = SPI_STATE_TRANSMITTING;
            XSpi_Transfer(&interface->hwInterface, interface->writeBuffer, interface->readBuffer, writeLength);
            status = SPI_STATUS_TX_STARTED;
        }
    }
    exitCriticalRegion(crdata);

    return status;
}


SpiStatus spiReadData(SpiInterface* interface, uint8* readBuffer, uint16 maxReadLength, uint16* readLength)
{
    SpiStatus status;
    
    ASSERT(interface);
    ASSERT(readBuffer);
    ASSERT(maxReadLength <= SPI_BUFFER_SIZE);
    ASSERT(readLength);
    
    CRData crdata = enterCriticalRegion();
    {
        if(interface->state == SPI_STATE_TRANSMITTING)
        {
            status = SPI_STATUS_ERROR_TX_IN_PROCESS;
        }
        else if(interface->state == SPI_STATE_DONE_WITH_ERRORS)
        {
            status = SPI_STATUS_TX_ERROR;
        }
        else if(interface->state == SPI_STATE_DONE)
        {
            if(maxReadLength < interface->readLength)
            {
                status      = SPI_STATUS_ERROR_RX_OVERRUN;
                *readLength = maxReadLength;
            }
            else
            {
                status      = SPI_STATUS_RX_OK;
                *readLength = interface->readLength;
            }

            dataCopy(interface, readBuffer, interface->readBuffer, *readLength);

            interface->state = SPI_STATE_IDLE;
        }
        else
        {
            status      = SPI_STATUS_ERROR_NO_RX_AVAILABLE;
            *readLength = 0;
        }
    }
    exitCriticalRegion(crdata);
    
    return status;
}



SpiStatus spiWaitAndStartTransmit(SpiInterface* interface, uint8* writeBuffer, uint16 writeLength, uint32 timeout_us)
{
    ASSERT(interface);
    spiWaitForIdle(interface, timeout_us);
    return spiStartTransmit(interface, writeBuffer, writeLength);
}



SpiStatus spiWaitAndReadData(SpiInterface* interface, uint8* readBuffer, uint16 maxReadLength, uint16* readLength, uint32 timeout_us)
{
    ASSERT(interface);
    spiWaitForReady(interface, timeout_us);
    return spiReadData(interface, readBuffer, maxReadLength, readLength);
}



void spiReset(SpiInterface* interface)
{
    ASSERT(interface);
    XSpi_Reset(&interface->hwInterface);
}


void spiSetOptions(SpiInterface* interface, uint32 xilOptions)
{
    ASSERT(XSpi_SetOptions(&interface->hwInterface, xilOptions) == XST_SUCCESS);
}


///////////////////////////////////////////////////
// Local functions

static void dataCopy(SpiInterface* interface, uint8* toBuf, uint8* fromBuf, uint32 count)
{
    if(interface->invertedDataCopy)
    {
        int i;
        for(i = 0; i < count; i++)
        {
            toBuf[i] = ~fromBuf[i];
        }
    }
    else
    {
        memcpy(toBuf, fromBuf, count);
    }
}



static void spiInterruptHandler(void *callBackRef, Xuint32 statusEvent, Xuint32 byteCount)
{
    ASSERT(callBackRef);
    
    SpiInterface* interface = (SpiInterface*)callBackRef;
    
    if(statusEvent != XST_SPI_TRANSFER_DONE)
    {
        interface->state = SPI_STATE_DONE_WITH_ERRORS;
        interface->readLength = 0;
    }
    else
    {
        interface->state = SPI_STATE_DONE;
        interface->readLength = byteCount;
    }
}


// EOF

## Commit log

2015-01-20 Initial mechanical commit
    Mechanical drawings and datasheets
    [91259A109.SLDPRT, 94125K839.SLDPRT, RSR9KM21957_50030_800_2_03.stp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]
2015-01-20 Initial electronics commit
    Spec sheets and schematics for electronics
2015-01-20 Removing unneeded file
    On the mechanical submit I accidentally submitted a bad file
    [export.stp]
2015-01-20 Added air cylinder mechanical drawings
    Added air cylinder mechanical drawings
    [1.sldprt, 2.sldprt, 3.sldprt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]
2015-01-28 More Spec Sheets
    Added spec sheets for mechanical parts when I could find them or just
    screen shots of specs if documents weren't available. Added
    instructions on how to set up block diagrams so we are consistent. I
    also put readmes in empty folders so the folder structure will show up
    for everyone
    [Motor_Drive.PcbDoc, Motor_Drive.PcbLib, Motor_Drive.PrjPCB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]
2015-01-30 Reader Control Panel
    Reader Control Panel is the gui application that interacts with the
    system control board. We will eventually rename this and do some more
    gutting but most of it has been gutted
2015-02-02 Assembly with frame
    Assembly with frame
    [10-10 frame.SLDPRT, 10-20 frame.SLDPRT, 22050579406.SLDPRT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]
2015-02-02 Herbert Controller
    Mostly all gutted now to just what we need. Still need to add event
    handlers for the buttons. Name changed to Herbert Controller. Version
    set to 0.01
2015-02-03 System Control FW Version 0.03
    Changed the comm interface for move relatives to make face characters.
    Also changed the stepper motor frequency from 2000 to 1500, in the
    future we would like to calibrate this value and store it in flash.
2015-02-03 Herbert Controller Version 0.02
    Added command handlers for the motor move buttons
2015-02-03 Added actuate arms
    Added the event handlers for the in and out buttons for actuating the
    arms
2015-02-09 Added Driver files.
2015-02-18 2nd attempt at getting switches integrated
2015-04-19 Added Stepper Motor Section
2015-04-22 Revised proposal 'Electro-mechanical stepper' section.
2015-04-29 added sections for the actuator and stepper motors.
2015-06-15 Finished Up Switch Firmware
2015-06-26 Added kcube, Updated fgpa switches to include pulldowns, updated firmware
2015-06-26 Mechanical Updates
    [Assem1.SLDASM, bearing plateform2.SLDPRT]
2015-09-29 Fixed error in test switch print Added files to gitignore
2015-10-15 Cleaned up unused code. Fixed order of relays to match set configuration.
2015-11-25 added sample image
2015-12-10 Added Arm Initialization
    This commit includes the code necessary to initialize the arms.
2015-12-17 Added final presentation and supporting material.
    This commit includes the PowerPoint that we used in our final
    presentation, along with the supporting material used in the
    presentation.
2015-12-17 Cleaned up files, added readmes
    [BearingPlateform2.DWG, RubenCubanBoM.xlsx, SolenoidValveMount.DWG]
2015-12-18 arm progression and break sensors
